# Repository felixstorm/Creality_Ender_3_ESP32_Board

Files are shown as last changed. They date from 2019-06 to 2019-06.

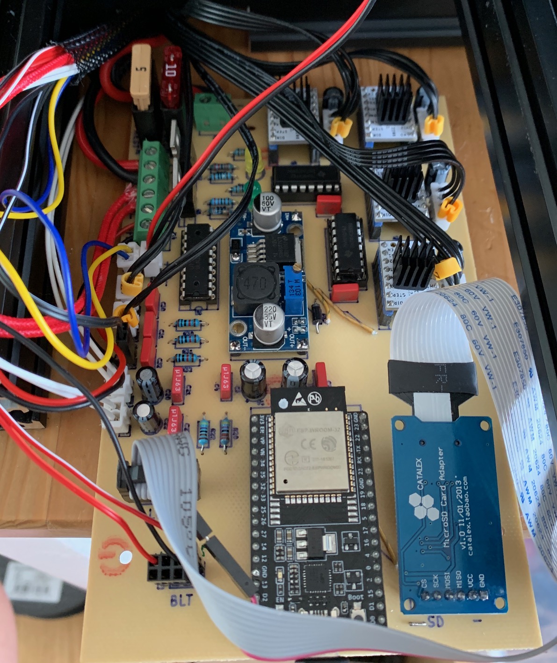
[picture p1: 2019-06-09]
Creality_Ender_3_ESP32_Board.jpg

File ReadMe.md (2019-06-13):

# ESP32 RepRap Controller Board for Creality Ender 3

**Use at your own risk! This is just a personal project and work in progress, and I do not have any professional experience in this field. And although it does work nicely for me, the power supply and heaters have enough power to set your house on fire if not used correctly. Therefore be sure to think about the stuff you do yourself and respect all the necessary safety precautions!**

This is a bare minimum RepRap mainboard that I created for my own Creality Ender 3, heavily based on the work of [Simon Jouet](https://github.com/simon-jouet).  
He did a great job developing the HAL for the ESP32 for [Marlin](https://github.com/MarlinFirmware/Marlin/tree/bugfix-2.0.x/Marlin/src/HAL/HAL_ESP32) including the use of I2S and shift registers to drive the stepper drivers. I2S needs very little hardware overhead, but increases the somewhat limited number of GPIOs on the ESP32 significantly, allowing to also connect the stock Ender 3 display as well as a BLTouch and also parts cooling, control board and hotend fans independently. Additionally it provides perfect stepper timing (based on the ESP32's internal I2S clock).  
He also developed his own [ESP32 controller](https://github.com/simon-jouet/ESP32Controller) which this board is heavily based on.

This is the third iteration of the board, and although it has only been in use for a few hours yet, it does seem to work nicely in every respect. Will post updates here...

## Technical Notes
* The board is the bare minimum to help my Ender 3 to a 32 bit brain and WiFi. I use breakout boards wherever it makes sense to reduce complexity as much as possible. It is not primarly geared towards low cost, but towards little effort (although it took more of it than I hoped for in the beginning ;-) ).
* The board is through hole and single sided with a few wire bridges. This is because I am so old that I am more used to THT than SMD, because most stuff is on on breakout boards anyway and because I wanted to mill the board on my CNC.
* There is a [PDF](https://github.com/felixstorm/Creality_Ender_3_ESP32_Board/blob/master/201904_Esp32ReprapController_Schematic_and_Layout.pdf) with schematic and board layout and a [photo of my board](https://github.com/felixstorm/Creality_Ender_3_ESP32_Board/blob/master/Creality_Ender_3_ESP32_Board.jpg) available to get a quick look.
* The board is larger (100 x 160 mm) than the stock Ender 3 mainboard, so you will need (to print) a different case for it. I will probably develop one some time, put it on Thingiverse and then link it from here.
* SD card reader: I am using a microSD to regular SD extension and have the SD card reader mounted behind the display, so I used a microSD breakout board with the slot oriented inwards where I just plug in the extension cable. The board used to be 5V, but I shorted the voltage regulator with some solder to make it work with 3.3V.
* Stepper Drivers: I use TMC2208 because they are quiet and relatively cheap. Since I am not interested in any tuning here, I hard-wired it's configuration pins. In case you want to use different drivers, you might have to cut traces on these pins or change the layout.
* I have yet to make use of WiFi. My plan is to use [ESP3D](https://github.com/luc-github/ESP3D) with Marlin integrated at some point in time, but I have yet to figure out how far Luc as gotten with the integration of ESP3 into [Marlin](https://github.com/luc-github/Marlin/tree/bugfix-2.0.x).
* The board should run stock [Marlin for ESP32](https://github.com/MarlinFirmware/Marlin/tree/bugfix-2.0.x/Marlin/src/HAL/HAL_ESP32) (as my minor pull requests have all been merged now). For reference, my current personal setup including my complete configuration is available [here](https://github.com/felixstorm/Marlin/tree/Felix_Ender3_ESP32_2.0.x).
* In case you create your own board / layout, be sure to take special care of the I2S lines. The first two variants of my board also did work somehow, but the temperature readings were really, really noisy (jumping up and down wildly by 5-8 °C). It turned out that this was caused by my really poor routing of the I2S lines which injected lots of noise into VCC. The second iteration was better, but there was still more noise than I had hoped for, so I took more time for the layout of board revision r3, moved components and switched pins to separate I2S far from VCC and analog pins and to reduce the complexity of the layout, routed all power and analog lines by hand, placed a ground plane around the I2S lines and left only standard digital lines for the auto-router.
* I used [KiCad](http://www.kicad-pcb.org/) for the schematic and the board and [TopoR Lite](https://www.eremex.com/products/topor/) for auto-routing. TopoR works quite well, is available for free with some (totally acceptable) limitations and was pretty helpful as it also has a special single-sided mode, even though it took some time to get used to.
* For milling, I used [pcb2gcode](https://github.com/pcb2gcode/pcb2gcode), which also worked well for me since it allows to add safety margins easily by setting a cutter width larger than the actual cutter. It will still mill between traces that are closer together than theoretically possible with the specified cutter width (which [FlatCAM](http://flatcam.org/) unfortunately does not do), but leaves all other traces wider. And although it is command-line only, one can put all settings in a config file per project and it does dump out nice SVG files where it illustrates its calculations.

## License: MIT

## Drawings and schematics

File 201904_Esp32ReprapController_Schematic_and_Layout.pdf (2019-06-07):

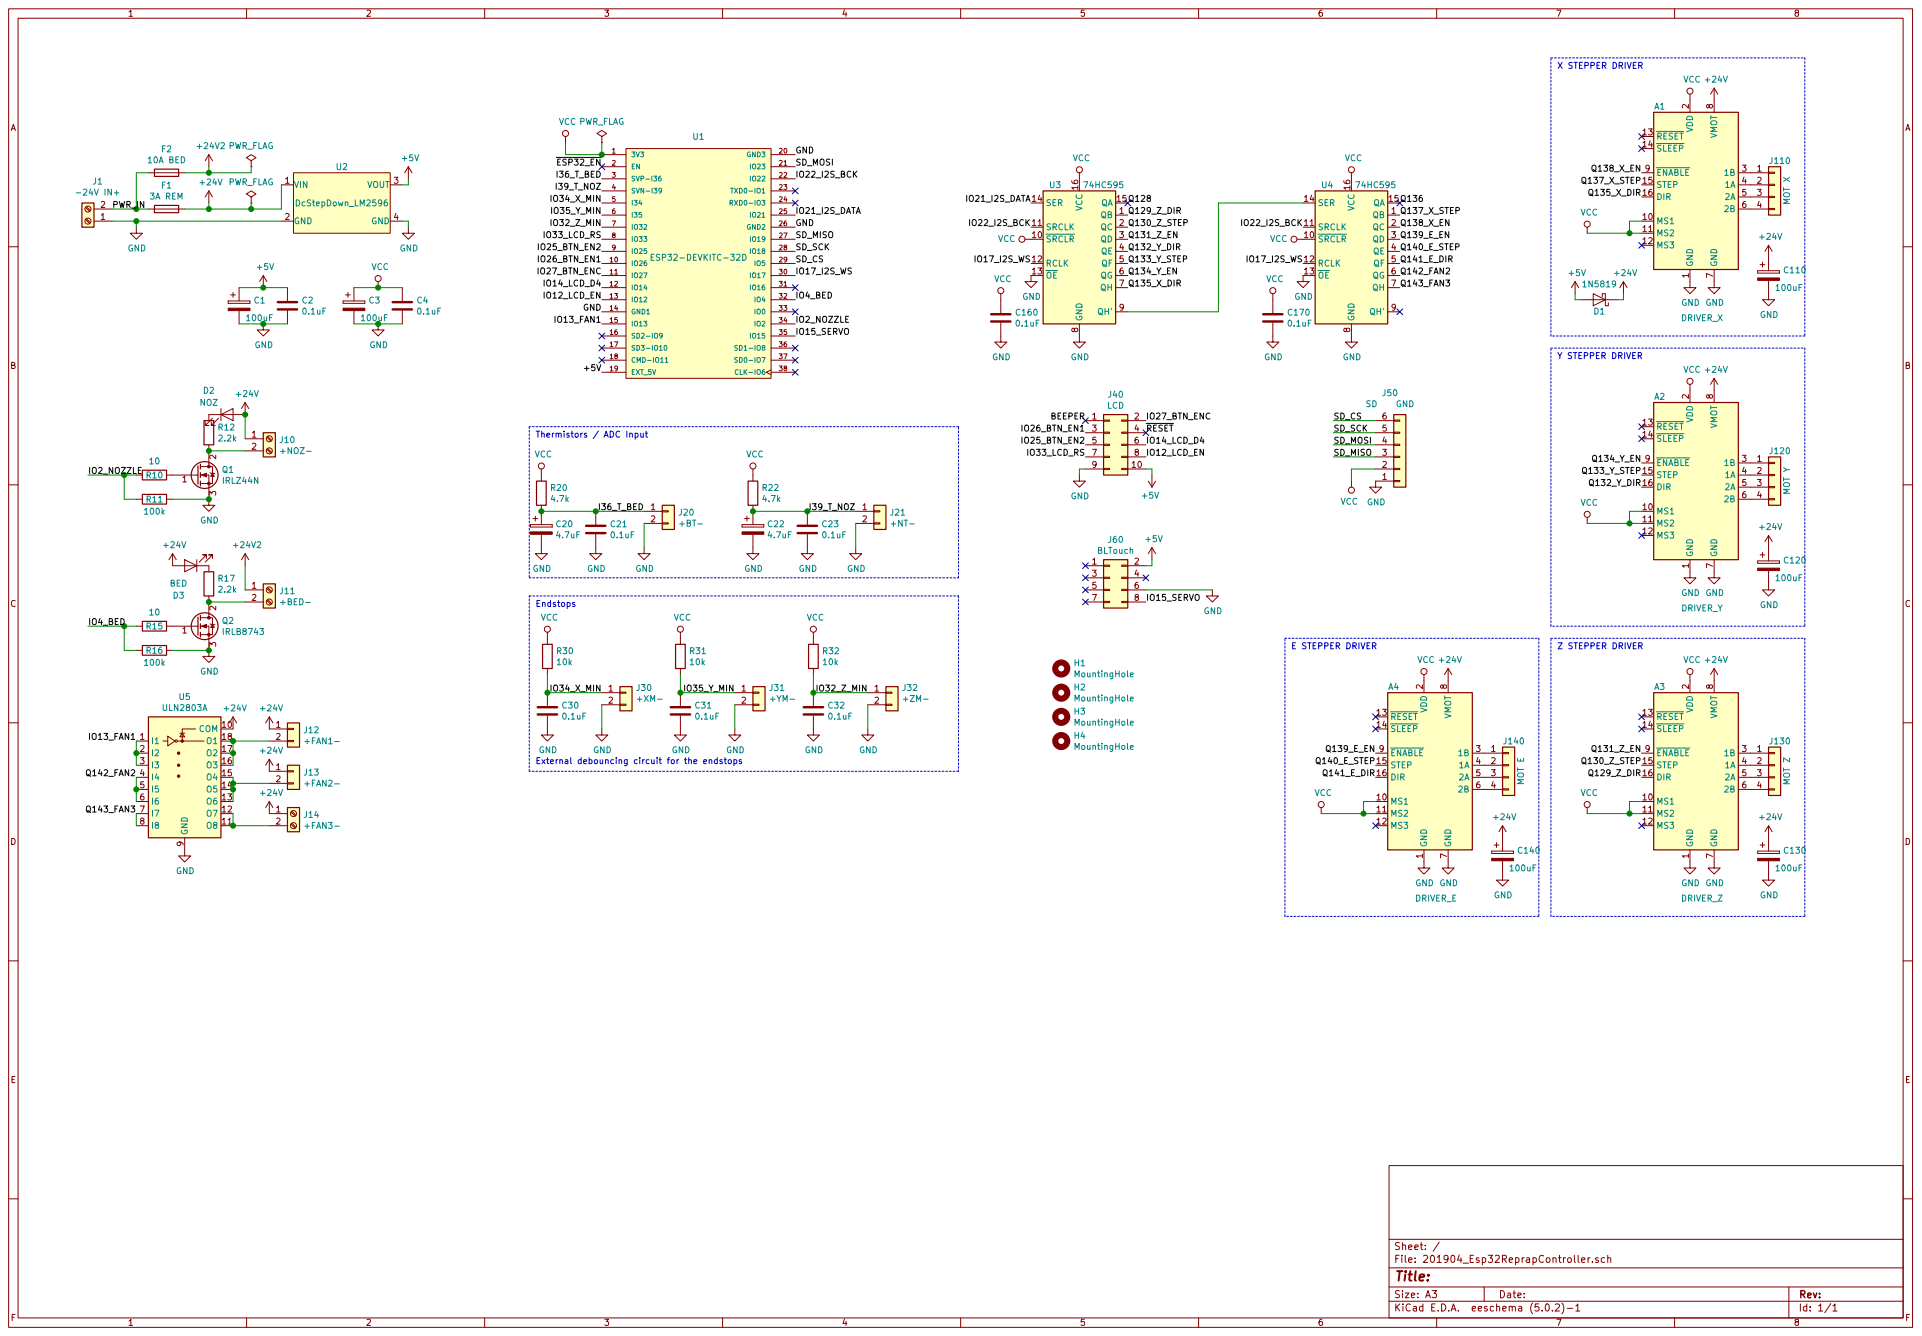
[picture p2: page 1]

1 MS1 10 MS2 11 MS3 12 RESET 13 SLEEP 14 STEP 15 DIR 16 VDD

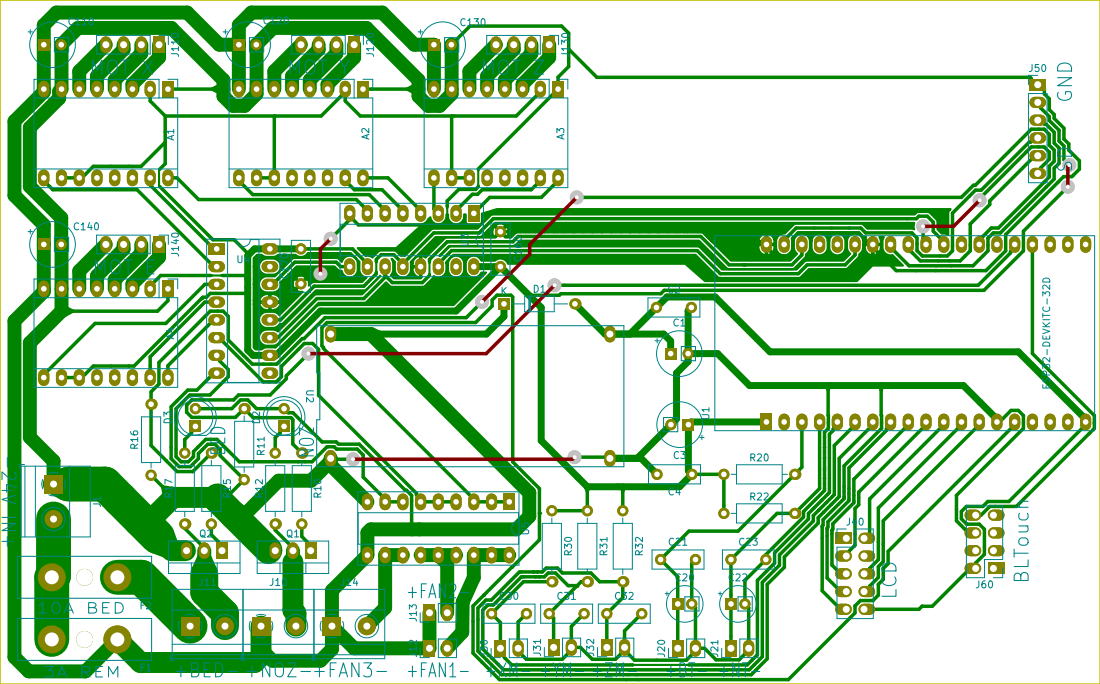
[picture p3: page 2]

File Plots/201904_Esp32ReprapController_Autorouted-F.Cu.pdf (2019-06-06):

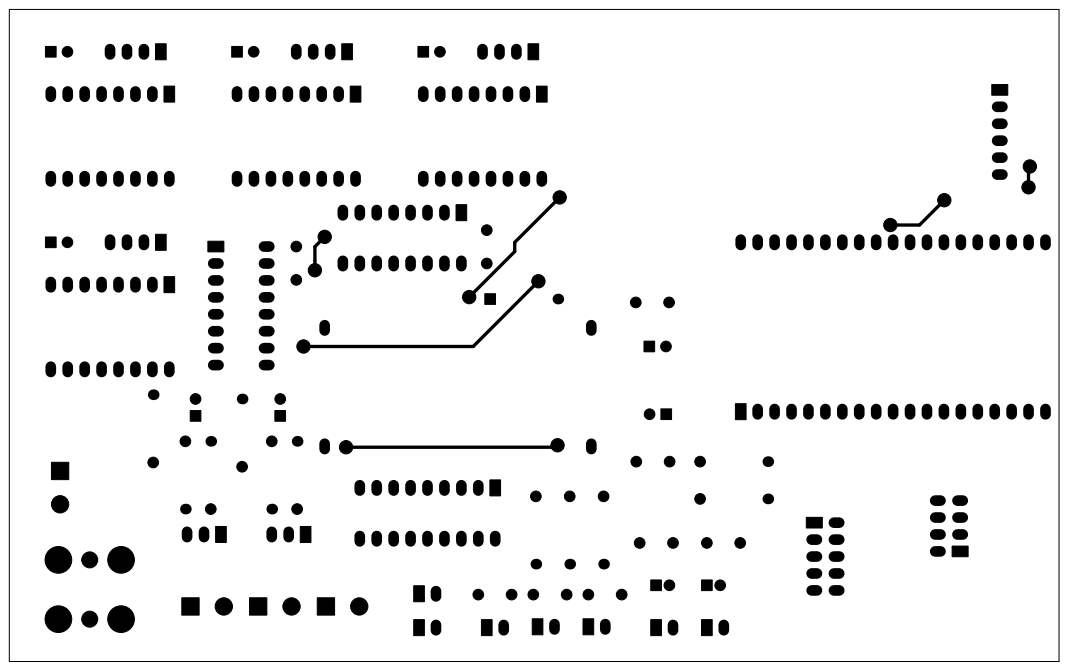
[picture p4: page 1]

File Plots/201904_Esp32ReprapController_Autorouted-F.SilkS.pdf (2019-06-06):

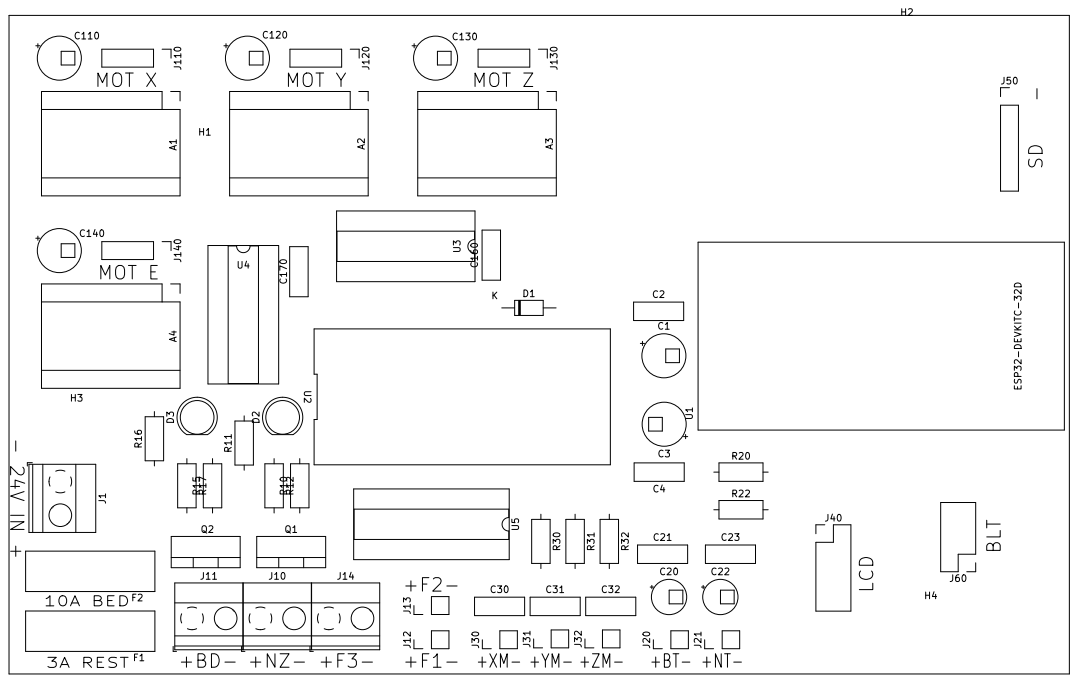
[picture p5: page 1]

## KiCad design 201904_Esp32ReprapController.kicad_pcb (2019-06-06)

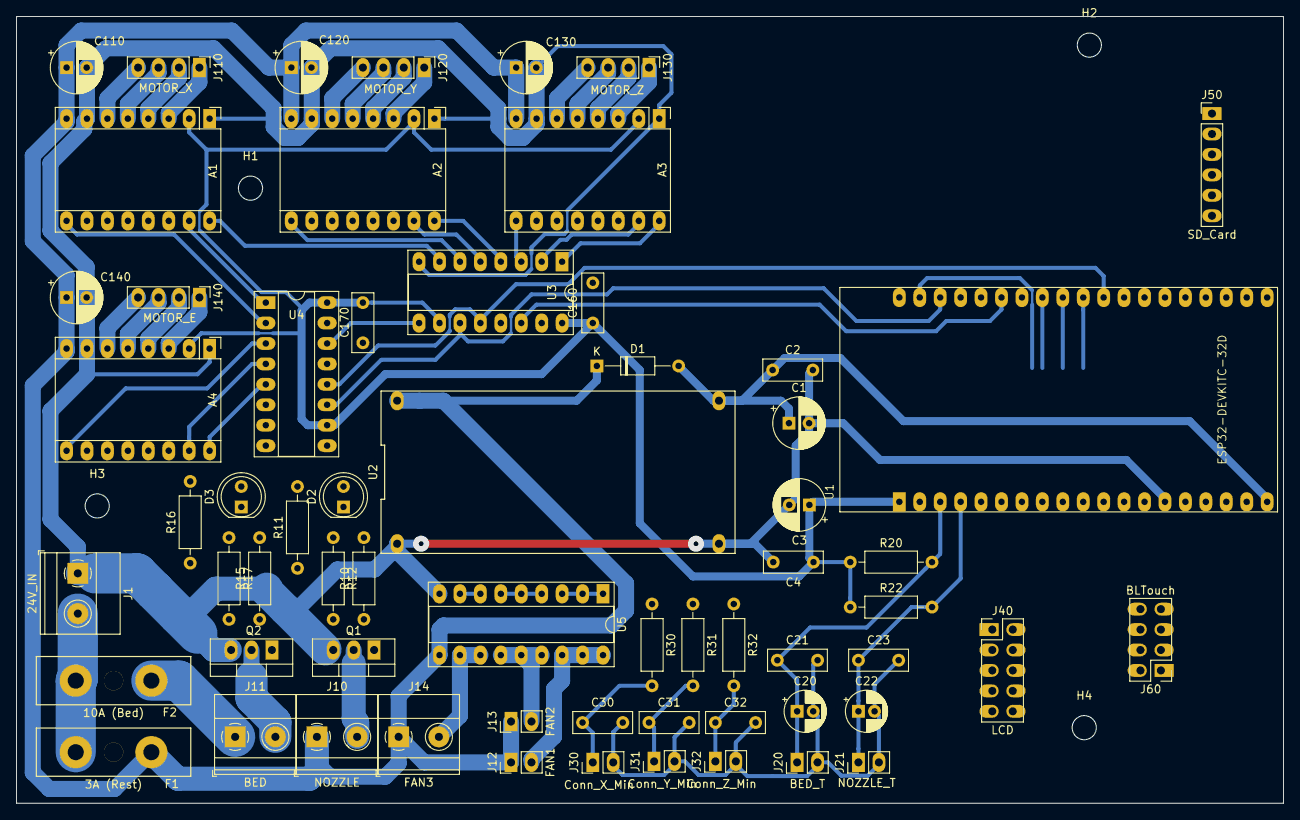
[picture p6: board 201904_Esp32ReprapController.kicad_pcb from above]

Board: 2 copper layers, 157.5 x 97.8 mm, 66 parts (0 on the bottom side), 68 nets.

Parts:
A1: DRIVER_X; Pololu_Breakout-16_15.2x20.3mm_LongPads
A2: DRIVER_Y; Pololu_Breakout-16_15.2x20.3mm_LongPads
A3: DRIVER_Z; Pololu_Breakout-16_15.2x20.3mm_LongPads
A4: DRIVER_E; Pololu_Breakout-16_15.2x20.3mm_LongPads
C1, C3, C110, C120, C130, C140: 100uF; CP_Radial_D6.3mm_P2.50mm
C2, C4, C21, C23, C30, C31, C32, C160, C170: 0.1uF; C_Rect_L7.2mm_W2.5mm_P5.00mm_FKS2_FKP2_MKS2_MKP2
C20, C22: 4.7uF; CP_Radial_D5.0mm_P2.00mm
D1: 1N5819; D_DO-35_SOD27_P10.16mm_Horizontal
D2: LED_NOZ; LED_D5.0mm
D3: LED_BED; LED_D5.0mm
F1: 3A (Rest); Fuse_ESKA_380.000
F2: 10A (Bed); Fuse_ESKA_380.000
H1, H2, H3, H4: MountingHole; MountingHole_3mm
J1: 24V_IN; TerminalBlock_ScrewTerminal_1x02_P5.00mm_Horizontal
J10: NOZZLE; TerminalBlock_ScrewTerminal_1x02_P5.00mm_Horizontal
J11: BED; TerminalBlock_ScrewTerminal_1x02_P5.00mm_Horizontal
J12: FAN1; PinHeader_1x02_P2.54mm_Vertical_LongPads
J13: FAN2; PinHeader_1x02_P2.54mm_Vertical_LongPads
J14: FAN3; TerminalBlock_ScrewTerminal_1x02_P5.00mm_Horizontal
J20: BED_T; PinHeader_1x02_P2.54mm_Vertical_LongPads
J21: NOZZLE_T; PinHeader_1x02_P2.54mm_Vertical_LongPads
J30: Conn_X_Min; PinHeader_1x02_P2.54mm_Vertical_LongPads
J31: Conn_Y_Min; PinHeader_1x02_P2.54mm_Vertical_LongPads
J32: Conn_Z_Min; PinHeader_1x02_P2.54mm_Vertical_LongPads
J40: LCD; PinHeader_2x05_P2.54mm_Vertical_LongPads
J50: SD_Card; PinHeader_1x06_P2.54mm_Vertical_LongPads
J60: BLTouch; PinHeader_2x04_P2.54mm_Vertical_LongPads
J110: MOTOR_X; PinHeader_1x04_P2.54mm_Vertical_LongPads
J120: MOTOR_Y; PinHeader_1x04_P2.54mm_Vertical_LongPads
J130: MOTOR_Z; PinHeader_1x04_P2.54mm_Vertical_LongPads
J140: MOTOR_E; PinHeader_1x04_P2.54mm_Vertical_LongPads
Q1: IRLZ44N; TO-220-3_Vertical_LongPads
Q2: IRLB8743; TO-220-3_Vertical_LongPads
R10, R15: 10; R_Axial_DIN0207_L6.3mm_D2.5mm_P10.16mm_Horizontal
R11, R16: 100k; R_Axial_DIN0207_L6.3mm_D2.5mm_P10.16mm_Horizontal
R12, R17: 2.2k; R_Axial_DIN0207_L6.3mm_D2.5mm_P10.16mm_Horizontal
R20, R22: 4.7k; R_Axial_DIN0207_L6.3mm_D2.5mm_P10.16mm_Horizontal
R30, R31, R32: 10k; R_Axial_DIN0207_L6.3mm_D2.5mm_P10.16mm_Horizontal
U1: ESP32-DEVKITC-32D; MODULE_ESP32-DEVKITC-32D_LongPads
U2: DcStepDown_LM2596; Module_LM2596_DC-DC
U3, U4: 74HC595; DIP-16_W7.62mm_Socket_LongPads
U5: ULN2803A; DIP-18_W7.62mm_Socket_LongPads

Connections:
+5V: C1.1, C2.1, D1.2, J40.10, J60.2, U1.19, U2.3
+24V: A1.8, A2.8, A3.8, A4.8, C110.1, C120.1, C130.1, C140.1, D1.1, D2.2, D3.2, F1.1, J10.1, J12.1, J13.1, J14.1, U2.1, U5.10
+24V2: F2.1, J11.1
/I36_T_BED: C20.1, C21.1, J20.1, R20.2, U1.3
/I39_T_NOZ: C22.1, C23.1, J21.1, R22.2, U1.4
/IO17_I2S_WS: U1.30, U3.12, U4.12
/IO21_I2S_BCK: U1.22, U3.11, U4.11
/IO22_I2S_DATA: U1.25, U3.14
/IOx_BED: R15.2, R16.2, U1.34
/IOx_BTN_EN1: J40.3, U1.8
/IOx_BTN_EN2: J40.5, U1.9
/IOx_BTN_ENC: J40.2, U1.10
/IOx_FAN1: U1.15, U5.1, U5.2, U5.3
/IOx_LCD_D4: J40.6, U1.11
/IOx_LCD_EN: J40.8, U1.13
/IOx_LCD_RS: J40.7, U1.12
/IOx_NOZZLE: R10.2, R11.2, U1.32
/IOx_SERVO: J60.8, U1.35
/IOx_X_MIN: C30.1, J30.1, R30.2, U1.5
/IOx_Y_MIN: C31.1, J31.1, R31.2, U1.6
/IOx_Z_MIN: C32.1, J32.1, R32.2, U1.7
/PWR_IN: F1.2, F2.2, J1.2
/Q129_Z_DIR: A3.16, U3.1
/Q130_Z_STEP: A3.15, U3.2
/Q131_Z_EN: A3.9, U3.3
/Q132_Y_DIR: A2.16, U3.4
/Q133_Y_STEP: A2.15, U3.5
/Q134_Y_EN: A2.9, U3.6
/Q135_X_DIR: A1.16, U3.7
/Q137_X_STEP: A1.15, U4.1
/Q138_X_EN: A1.9, U4.2
/Q139_E_EN: A4.9, U4.3
/Q140_E_STEP: A4.15, U4.4
/Q141_E_DIR: A4.16, U4.5
/Q142_FAN2: U4.6, U5.4, U5.5, U5.6
/Q143_FAN3: U4.7, U5.7, U5.8
/SD_CS: J50.6, U1.29
/SD_MISO: J50.3, U1.27
/SD_MOSI: J50.4, U1.21
/SD_SCK: J50.5, U1.28
GND: A1.1, A1.7, A2.1, A2.7, A3.1, A3.7, A4.1, A4.7, C1.2, C2.2, C3.2, C4.2, C20.2, C21.2, C22.2, C23.2, C30.2, C31.2, C32.2, C110.2, C120.2, C130.2, C140.2, C160.2, C170.2, J1.1, J20.2, J21.2, J30.2, J31.2, J32.2, J40.9, J50.1, J60.6, Q1.3, Q2.3, R11.1, R16.1, U1.14, U1.20, U1.26, U2.2, U2.4, U3.8, U3.13, U4.8, U4.13, U5.9
unnamed: A1.3, J110.1
unnamed: A1.4, J110.2
unnamed: A1.5, J110.3
unnamed: A1.6, J110.4
unnamed: A2.3, J120.1
unnamed: A2.4, J120.2
unnamed: A2.5, J120.3
unnamed: A2.6, J120.4
unnamed: A3.3, J130.1
unnamed: A3.4, J130.2
unnamed: A3.5, J130.3
unnamed: A3.6, J130.4
unnamed: A4.3, J140.1
unnamed: A4.4, J140.2
unnamed: A4.5, J140.3
unnamed: A4.6, J140.4
unnamed: D2.1, R12.1
unnamed: D3.1, R17.1
unnamed: J10.2, Q1.2, R12.2
unnamed: J11.2, Q2.2, R17.2
unnamed: J12.2, U5.16, U5.17, U5.18
unnamed: J13.2, U5.13, U5.14, U5.15
unnamed: J14.2, U5.11, U5.12
unnamed: Q1.1, R10.1
unnamed: Q2.1, R15.1
unnamed: U3.9, U4.14
VCC: A1.2, A1.10, A1.11, A2.2, A2.10, A2.11, A3.2, A3.10, A3.11, A4.2, A4.10, A4.11, C3.1, C4.1, C160.1, C170.1, J50.2, R20.1, R22.1, R30.1, R31.1, R32.1, U1.1, U3.10, U3.16, U4.10, U4.16

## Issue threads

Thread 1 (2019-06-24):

Error compiling for CR10_STOCKDISPLAY

vivian-ng, 2019-06-24:
Thank you for the work done on Marlin firmware to fix many stuff on the ESP32 HAL.

I tried to compile bugfix-2.0.x which has all your changes, but when I try to compile for CR10_STOCKDISPLAY (the one that Ender-3 uses, right?), I get the following error. I was wondering how you went around this error.

I have U8glib 1.19.1 installed.

```
In file included from /tmp/arduino_build_790171/sketch/src/lcd/dogm/../../inc/MarlinConfigPre.h:32:0,
                 from /tmp/arduino_build_790171/sketch/src/lcd/dogm/../../inc/MarlinConfig.h:28,
                 from /tmp/arduino_build_790171/sketch/src/lcd/dogm/ultralcd_st7920_u8glib_rrd_AVR.cpp:26:
/tmp/arduino_build_790171/sketch/src/lcd/dogm/ultralcd_st7920_u8glib_rrd_AVR.cpp: In function 'void ST7920_SWSPI_SND_8BIT(uint8_t)':
/tmp/arduino_build_790171/sketch/src/lcd/dogm/ultralcd_st7920_u8glib_rrd_AVR.h:33:25: error: 'LCD_PINS_ENABLE' was not declared in this scope
 #define ST7920_DAT_PIN  LCD_PINS_ENABLE
                         ^
/tmp/arduino_build_790171/sketch/src/lcd/dogm/../../inc/../core/macros.h:77:23: note: in definition of macro 'TEST'
 #define TEST(n,b) !!((n)&_BV(b))
                       ^
/tmp/arduino_build_790171/sketch/src/lcd/dogm/../../inc/../HAL/HAL_ESP32/fastio_ESP32.h:47:34: note: in expansion of macro 'IS_I2S_EXPANDER_PIN'
 #define WRITE(IO, v)            (IS_I2S_EXPANDER_PIN(IO) ? i2s_write(I2S_EXPANDER_PIN_INDEX(IO), v) : digitalWrite(IO, v))
                                  ^
/tmp/arduino_build_790171/sketch/src/lcd/dogm/ultralcd_st7920_u8glib_rrd_AVR.cpp:47:3: note: in expansion of macro 'WRITE'
   WRITE(ST7920_DAT_PIN, val & 0x80); ST7920_DELAY_2; \
   ^
/tmp/arduino_build_790171/sketch/src/lcd/dogm/ultralcd_st7920_u8glib_rrd_AVR.cpp:47:9: note: in expansion of macro 'ST7920_DAT_PIN'
   WRITE(ST7920_DAT_PIN, val & 0x80); ST7920_DELAY_2; \
         ^
/tmp/arduino_build_790171/sketch/src/lcd/dogm/ultralcd_st7920_u8glib_rrd_AVR.cpp:55:3: note: in expansion of macro 'ST7920_SND_BIT'
   ST7920_SND_BIT; // 1
   ^
In file included from /tmp/arduino_build_790171/sketch/src/lcd/dogm/../../inc/../HAL/HAL_ESP32/HAL.h:37:0,
                 from /tmp/arduino_build_790171/sketch/src/lcd/dogm/../../inc/MarlinConfig.h:30,
                 from /tmp/arduino_build_790171/sketch/src/lcd/dogm/ultralcd_st7920_u8glib_rrd_AVR.cpp:26:
/tmp/arduino_build_790171/sketch/src/lcd/dogm/ultralcd_st7920_u8glib_rrd_AVR.cpp: In function 'uint8_t u8g_dev_rrd_st7920_128x64_fn(u8g_t*, u8g_dev_t*, uint8_t, void*)':
/tmp/arduino_build_790171/sketch/src/lcd/dogm/ultralcd_st7920_u8glib_rrd_AVR.h:34:25: error: 'LCD_PINS_RS' was not declared in this scope
 #define ST7920_CS_PIN   LCD_PINS_RS
                         ^
/tmp/arduino_build_790171/sketch/src/lcd/dogm/../../inc/../HAL/HAL_ESP32/fastio_ESP32.h:38:41: note: in definition of macro '_SET_OUTPUT'
 #define _SET_OUTPUT(IO)         pinMode(IO, OUTPUT)
                                         ^
/tmp/arduino_build_790171/sketch/src/lcd/dogm/ultralcd_st7920_u8glib_rrd_AVR.cpp:69:7: note: in expansion of macro 'OUT_WRITE'
       OUT_WRITE(ST7920_CS_PIN, LOW);
       ^
/tmp/arduino_build_790171/sketch/src/lcd/dogm/ultralcd_st7920_u8glib_rrd_AVR.cpp:69:17: note: in expansion of macro 'ST7920_CS_PIN'
       OUT_WRITE(ST7920_CS_PIN, LOW);
                 ^
/tmp/arduino_build_790171/sketch/src/lcd/dogm/ultralcd_st7920_u8glib_rrd_AVR.h:33:25: error: 'LCD_PINS_ENABLE' was not declared in this scope
 #define ST7920_DAT_PIN  LCD_PINS_ENABLE
                         ^
/tmp/arduino_build_790171/sketch/src/lcd/dogm/../../inc/../HAL/HAL_ESP32/fastio_ESP32.h:38:41: note: in definition of macro '_SET_OUTPUT'
 #define _SET_OUTPUT(IO)         pinMode(IO, OUTPUT)
                                         ^
/tmp/arduino_build_790171/sketch/src/lcd/dogm/ultralcd_st7920_u8glib_rrd_AVR.cpp:70:7: note: in expansion of macro 'OUT_WRITE'
       OUT_WRITE(ST7920_DAT_PIN, LOW);
       ^
/tmp/arduino_build_790171/sketch/src/lcd/dogm/ultralcd_st7920_u8glib_rrd_AVR.cpp:70:17: note: in expansion of macro 'ST7920_DAT_PIN'
       OUT_WRITE(ST7920_DAT_PIN, LOW);
                 ^
In file included from /tmp/arduino_build_790171/sketch/src/lcd/dogm/../../inc/MarlinConfigPre.h:32:0,
                 from /tmp/arduino_build_790171/sketch/src/lcd/dogm/../../inc/MarlinConfig.h:28,
                 from /tmp/arduino_build_790171/sketch/src/lcd/dogm/ultralcd_st7920_u8glib_rrd_AVR.cpp:26:
/tmp/arduino_build_790171/sketch/src/lcd/dogm/ultralcd_st7920_u8glib_rrd_AVR.h:34:25: error: 'LCD_PINS_RS' was not declared in this scope
 #define ST7920_CS_PIN   LCD_PINS_RS
                         ^
/tmp/arduino_build_790171/sketch/src/lcd/dogm/../../inc/../core/macros.h:77:23: note: in definition of macro 'TEST'
 #define TEST(n,b) !!((n)&_BV(b))
                       ^
/tmp/arduino_build_790171/sketch/src/lcd/dogm/../../inc/../HAL/HAL_ESP32/fastio_ESP32.h:47:34: note: in expansion of macro 'IS_I2S_EXPANDER_PIN'
 #define WRITE(IO, v)            (IS_I2S_EXPANDER_PIN(IO) ? i2s_write(I2S_EXPANDER_PIN_INDEX(IO), v) : digitalWrite(IO, v))
                                  ^
/tmp/arduino_build_790171/sketch/src/lcd/dogm/ultralcd_st7920_u8glib_rrd_AVR.h:90:36: note: in expansion of macro 'WRITE'
 #define ST7920_CS()              { WRITE(ST7920_CS_PIN,1); U8G_DELAY(); }
                                    ^
/tmp/arduino_build_790171/sketch/src/lcd/dogm/ultralcd_st7920_u8glib_rrd_AVR.h:90:42: note: in expansion of macro 'ST7920_CS_PIN'
 #define ST7920_CS()              { WRITE(ST7920_CS_PIN,1); U8G_DELAY(); }
                                          ^
/tmp/arduino_build_790171/sketch/src/lcd/dogm/ultralcd_st7920_u8glib_rrd_AVR.cpp:73:7: note: in expansion of macro 'ST7920_CS'
       ST7920_CS();
       ^
/tmp/arduino_build_790171/sketch/src/lcd/dogm/ultralcd_st7920_u8glib_rrd_AVR.h:34:25: error: 'LCD_PINS_RS' was not declared in this scope
 #define ST7920_CS_PIN   LCD_PINS_RS
                         ^
/tmp/arduino_build_790171/sketch/src/lcd/dogm/../../inc/../core/macros.h:77:23: note: in definition of macro 'TEST'
 #define TEST(n,b) !!((n)&_BV(b))
                       ^
/tmp/arduino_build_790171/sketch/src/lcd/dogm/../../inc/../HAL/HAL_ESP32/fastio_ESP32.h:47:34: note: in expansion of macro 'IS_I2S_EXPANDER_PIN'
 #define WRITE(IO, v)            (IS_I2S_EXPANDER_PIN(IO) ? i2s_write(I2S_EXPANDER_PIN_INDEX(IO), v) : digitalWrite(IO, v))
                                  ^
/tmp/arduino_build_790171/sketch/src/lcd/dogm/ultralcd_st7920_u8glib_rrd_AVR.h:91:36: note: in expansion of macro 'WRITE'
 #define ST7920_NCS()             { WRITE(ST7920_CS_PIN,0); }
                                    ^
/tmp/arduino_build_790171/sketch/src/lcd/dogm/ultralcd_st7920_u8glib_rrd_AVR.h:91:42: note: in expansion of macro 'ST7920_CS_PIN'
 #define ST7920_NCS()             { WRITE(ST7920_CS_PIN,0); }
                                          ^
/tmp/arduino_build_790171/sketch/src/lcd/dogm/ultralcd_st7920_u8glib_rrd_AVR.cpp:91:7: note: in expansion of macro 'ST7920_NCS'
       ST7920_NCS();
       ^
/tmp/arduino_build_790171/sketch/src/lcd/dogm/ultralcd_st7920_u8glib_rrd_AVR.h:34:25: error: 'LCD_PINS_RS' was not declared in this scope
 #define ST7920_CS_PIN   LCD_PINS_RS
                         ^
/tmp/arduino_build_790171/sketch/src/lcd/dogm/../../inc/../core/macros.h:77:23: note: in definition of macro 'TEST'
 #define TEST(n,b) !!((n)&_BV(b))
                       ^
/tmp/arduino_build_790171/sketch/src/lcd/dogm/../../inc/../HAL/HAL_ESP32/fastio_ESP32.h:47:34: note: in expansion of macro 'IS_I2S_EXPANDER_PIN'
 #define WRITE(IO, v)            (IS_I2S_EXPANDER_PIN(IO) ? i2s_write(I2S_EXPANDER_PIN_INDEX(IO), v) : digitalWrite(IO, v))
                                  ^
/tmp/arduino_build_790171/sketch/src/lcd/dogm/ultralcd_st7920_u8glib_rrd_AVR.h:90:36: note: in expansion of macro 'WRITE'
 #define ST7920_CS()              { WRITE(ST7920_CS_PIN,1); U8G_DELAY(); }
                                    ^
/tmp/arduino_build_790171/sketch/src/lcd/dogm/ultralcd_st7920_u8glib_rrd_AVR.h:90:42: note: in expansion of macro 'ST7920_CS_PIN'
 #define ST7920_CS()              { WRITE(ST7920_CS_PIN,1); U8G_DELAY(); }
                                          ^
/tmp/arduino_build_790171/sketch/src/lcd/dogm/ultralcd_st7920_u8glib_rrd_AVR.cpp:103:7: note: in expansion of macro 'ST7920_CS'
       ST7920_CS();
       ^
/tmp/arduino_build_790171/sketch/src/lcd/dogm/ultralcd_st7920_u8glib_rrd_AVR.h:34:25: error: 'LCD_PINS_RS' was not declared in this scope
 #define ST7920_CS_PIN   LCD_PINS_RS
                         ^
/tmp/arduino_build_790171/sketch/src/lcd/dogm/../../inc/../core/macros.h:77:23: note: in definition of macro 'TEST'
 #define TEST(n,b) !!((n)&_BV(b))
                       ^
/tmp/arduino_build_790171/sketch/src/lcd/dogm/../../inc/../HAL/HAL_ESP32/fastio_ESP32.h:47:34: note: in expansion of macro 'IS_I2S_EXPANDER_PIN'
 #define WRITE(IO, v)            (IS_I2S_EXPANDER_PIN(IO) ? i2s_write(I2S_EXPANDER_PIN_INDEX(IO), v) : digitalWrite(IO, v))
                                  ^
/tmp/arduino_build_790171/sketch/src/lcd/dogm/ultralcd_st7920_u8glib_rrd_AVR.h:91:36: note: in expansion of macro 'WRITE'
 #define ST7920_NCS()             { WRITE(ST7920_CS_PIN,0); }
                                    ^
/tmp/arduino_build_790171/sketch/src/lcd/dogm/ultralcd_st7920_u8glib_rrd_AVR.h:91:42: note: in expansion of macro 'ST7920_CS_PIN'
 #define ST7920_NCS()             { WRITE(ST7920_CS_PIN,0); }
                                          ^
/tmp/arduino_build_790171/sketch/src/lcd/dogm/ultralcd_st7920_u8glib_rrd_AVR.cpp:118:7: note: in expansion of macro 'ST7920_NCS'
       ST7920_NCS();
       ^
In file included from /tmp/arduino_build_790171/sketch/src/lcd/dogm/ultralcd_DOGM.cpp:42:0:
/tmp/arduino_build_790171/sketch/src/lcd/dogm/ultralcd_DOGM.h:50:36: error: 'LCD_PINS_ENABLE' was not declared in this scope
     #define U8G_PARAM LCD_PINS_D4, LCD_PINS_ENABLE, LCD_PINS_RS       // Number of stripes can be adjusted in ultralcd_st7920_u8glib_rrd.h with PAGE_HEIGHT
                                    ^
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
vivian-ng, 2019-06-24:
I managed to compile using PlatformIO instead of Arduino IDE. However, I get a blank lit screen when I enable the CR10_STOCKDISPLAY.

Are there any pins which must be specifically used for the display? Or will any GPIO do? Same for I2S; pins 25, 26, 27 (the ones that simon-jouet originally used) doesn't seem to work for me... the motor will jerk, then hum, but no motion.

felixstorm, 2019-06-25:
Display: In general, any IO pins should do (I selected mine based on best trace routing on the PCB). Maybe take a look at my [pins file](https://github.com/felixstorm/Marlin/blob/Felix_Ender3_ESP32_2.0.x/Marlin/src/pins/pins_ESP32_FS_ENDER3.h)?

I2S: As far as I remember, any IO pins should be ok here as well (and I am pretty sure that the ones simon-jouet originally used did work on my first board). I also had some trouble getting I2S to work, but in the end all issues were tiny shorts on my board due to milling FR2. What I did for troubleshooting was to play with the enable-pins since they are easy to control by g-code ([M017](http://marlinfw.org/docs/gcode/M017.html) and [M018](http://marlinfw.org/docs/gcode/M018.html)) and easy to measure. If they work, then I2S in general should be ok...

vivian-ng, 2019-06-25:
Thank you!
What can I say? I am stupid and careless.
My pin definition works. But in all that copy and paste as I was trying to cut and paste code, there were some lines which should have been commented out but were not, and some `#ifndef` which were mistakenly left as `#ifdef`.

Now that it seems to be working, the next step is to find time to do a test print!

felixstorm, 2019-06-25:
@vivian-ng No worries! I like this solution to the problem a lot better than having to solve issues in the code ;-)

Closed 2019-06-25.

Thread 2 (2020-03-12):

Thanks, and a Marlin Question

MitchBradley, 2020-03-12:
Thanks for this project.  I made my own version with a few changes to suit my needs .  2-sided board with ample ground and power planes, jumper and connector options to use external drivers or Pololu sockets, options to use SPI to TMC drivers, etc.  My repo is not yet up on GitHub yet, but will be soon.

I'm now debugging the board.  My question is this - how much has your Marlin fork diverged?  I'm wondering if I should start with your fork or the stock Marlin 2.0.  I'm an experienced bare-metal programmer and electrical engineer so either way I'm not too worried.  Just looking for the best starting point.

MitchBradley, 2020-03-12:
Nevermind.  I looked at all the diffs between your branch and latest Marlin.  It seems like I should use the latest Marlin with your Configuration.h, Configuration_adv.h, and pins file.  I did that and so far things are working.   Still lots of testing to go, but it's all good so far.

Closed 2020-03-12.

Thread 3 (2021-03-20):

Stepper not respond

agoy507, 2021-03-20:
I make your prototype board for my ender 3, then i flash with your configuration. but stepper not move.
whats wrong ?? i'm using A4988 driver, 74HC595N.

what 74HC595 different with 74HC595N ?
what the different ??

Closed 2021-03-29.

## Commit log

2019-05-12 board r1 (milled and built 2019-05)
    [201904_Esp32ReprapController.dsn, 201904_Esp32ReprapController.kicad_pcb, 201904_Esp32ReprapController.sch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]
2019-06-06 board r2 (never built)
    [201904_Esp32ReprapController.dsn, 201904_Esp32ReprapController.kicad_pcb, 201904_Esp32ReprapController.sch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]
2019-06-06 remove older stuff
    [201904_Esp32ReprapController.kicad_pcb, 201904_Esp32ReprapController.sch, 201904_Esp32ReprapController_mod.dsn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]
2019-06-06 board r3 (milled and built 2019-06)
    [201904_Esp32ReprapController.dsn, 201904_Esp32ReprapController.kicad_pcb, 201904_Esp32ReprapController.sch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]
